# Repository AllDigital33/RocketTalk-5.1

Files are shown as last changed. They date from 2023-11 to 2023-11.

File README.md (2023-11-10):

# Rocket Talk v5.1

This is a full-featured rocket flight computer for amateur and experimental rocketry that incorporates radio telemetry, GPS tracking, staging, pyro event control, FTS, camera control, and more.

Please read the Overview.PDF file attached for a detailed overview of the hardware and software solution.

The code in the repository is split between the vehicle code (Arduino / Teensy) and the base station code (iPad / iOS Swift). 

# Disclaimer

We started this radio telemetry project in 2016 to better track our rockets in the skies over the Mojave desert. It has gone through a dozen hardware iterations and over fifty test flights. We always intended to share it and open source it, but projects like these are never complete. There is lots of room for improvement.

We’ve decided to take a snapshot and share our progress, so student groups and other amateurs can learn, borrow, or reuse some of our ideas and our sloppy code.

We owe a lot to the rocketry community, the TRF board, and student groups out at FAR that have shared their ideas, code, and practices to make our project and launches better and safer. 

This was never meant to be or become a commercial project, so please don't ask. The components and approach are way more expensive than any other trackers on the market, so you are not saving money by building your own. The EggTimer, TeleMega, and many more solutions are reliable and battle tested solutions.

This is a passion project to create bi-directional telemetry, long-range tracking, and an easy to use iPad based field solution.  

# Summary

**VEHICLE BOARD:**
* Teensy 4.1 MCU (ARM M7)
* GPS
* Barometer
* Two Accelerometers
* Gyroscope
* Pyro relays x 4
* Camera power control
* 64Mb of flash storage + SD transfer
* Temperature monitoring
* Voltage monitoring
* Bi-directional radio comms / 1W LoRa 433 Mhz 

**IPAD HANDHELD BASE STATION:**
* Simple touch-based UI for data and tracking
* Voice (siri like) event and alert reporting
* Local base GPS 
* Magnetometer / bearing
* Satellite mapping (Apple Maps)
* Local logging and file storage 
* Wifi/Internet
* Bi-directional radio comms / 1W LoRa 433 Mhz

# Vehicle Board Current Technology Choices

* **Teensy 4.1:**  The T4.1 with its Arm Cortex-M7 is just insanely fast for an MCU and it is loaded with a lot of versatile GPIO. We started our project on other Arduino based MCUs. Our last one was the ESP32. In benchmarks, an ESP32 can increment an integer about 700K times a second. That seems fast until you see the T4.1 (or 4.0) increment an integer 242 million times a second (wowzers!). This provides for almost unlimited CPU cycles for anything you can dream up during flight. The real limitation becomes the I2C bus, communication speeds, serial speeds, etc.  
* **Flash Memory:** The T4.1 has a built-in SD card that we used for years for logging data, but ultimately we had too many SD errors during flight that crashed the logging thread, so we switched to a 64 Mb flash chip (W25Q512JV) or 256mb (W25N02KVZEIR). The flash chip solders to the Teensy 4.1 and we're using the native LittleFS file system that uses the flash memory similar to a SD card. For easy transfer of data to SD there is a utility sketch that can be run after the flight. 
* **GPS:**  We are using the Ublox Max-M10S with serial communication. The M10S has proven to be an exceptional GPS, especially when combined with a Maxtena Helicore antenna. We run the GPS serial ttl instead of I2C, so we can save our I2C bus for sensor sampling. These GPS units are still under ITAR regulations, so they have limitations above 100K (more research needed).
* **GPS Antenna** The Maxtena Helicore M1575HCT-22P-SMA antenna is a passive GPS antenna capable of locking in 24+ satelites before launch.  
* **Barometer:**  We are using the TE MS5607 barometer on I2C sampling at 40Hz. We were using the BME280, but found it very susceptible to RF interference. The MS5607 has been reliable (no RFI), tracks up to 110K feet in the baro chamber, but it has a noisier signal, especially on descent. We also have to do some code gymnastics to sample at 40 hz and allow the sampling thread (and I2C bus) to stay free.
* **Accelerometers:** We have an Analog Devices ADXL375 200G accelerometer and a ST LSM6DSO32 32G accelerometer. The 200G is good to catch all the really big stuff and we often exceed the 32G’s of the LSM6DS, but the LSB resolution is not as good in a 200G setting, so the ST provides better resolution and accuracy below 32G’s. We are sampling the accelerometers and the gyro at 400 hz on the I2C bus.
* **Gyro:** The ST LSM6DSO32 also has a built-in gyroscope. We are using that, along with quaternions to calculate the rocket attitude (tilt).
* **Radios:**  We have tried a number of different radios, but we are very happy with our 1 watt LoRa radios on 433 Mhz (==FCC amateur radio license required==). You can get similar radios in 900 Mhz that don’t require a license. But, you are in this deep, so take the time to get a license. We use the LoRa 6100Pro serial TTL radios from NiceRF in China. The Lora technology is great, as we can create a mesh network and add a third radio on a tower to act as a repeater. These have proven to be reliable up to 15 miles “peak to peak” on the ground (mountain test) and I’m certain they will go to 100K+ feet in the air with the right antennas.
* **Downlink Antenna:**  The choice of downlink antennas on the vehicle is almost more important than the radio. We’ve tried dozens of antennas. The best antenna for us is a simple homemade dipole antenna running vertical in the airframe. We’ve tried whip, inverted V, fractal, and more, but the dipole performs the best. We used to make them by hand, but now we print our diploe antennas onto a long thin custom PCBs and trim to tune them (about $2/each)
* **5V Regulator:**  We use two L4941BDT-TR 5v 1A regulators to power the Teensy and the Radio. We run a separate regulator for the radio to minimize RFI and RF blowback, as well, provide the radio with a full one amp of power. All of the pyro events are triggered directly off of the Lipo battery and do not go through the regulators. 
* **Pyro Drivers:** We are using Rohm BV1HD090FJ-CE2 automotive switching drivers for all of our pyro events. These are rated at 5.5A and provide over-current protection and they have a convenient status pin that provides continuity check back to the MCU. There are other drivers that can switch up to 10A, but these have served us well for hundreds of pyro events using commercial MJG e-matches.
* **Terminals:**  We use JST board connectors for the low voltage connections and screw terminals for the hazard connections (power, switch, pyros).
* **RFI Shielding:**  A powerful one watt downlink transmitter comes with benefits and issues. On the positive, it can drive a data signal loud and far, but on the negative side it also showers all the sensors, the I2C lines, and the MCU with lots of disruptive radio frequency interference. In earlier versions we had sensor issues, code execution glitches, and full core dumps due to RFI. So, the current v5.1 board incorporates extensive shielding measures to protect the sensors and the MCU including full RF shield, ferrites, PCB ground planes, and more.

# Vehicle Board Code Overview

The Teensy code is built from a single C sketch in the Arduino (Teensyduino) IDE. It utilizes some external libraries for sensors, but is otherwise self-contained in a single code file. 

The code is partitioned into three Teensy threads, mimicking three separate infinite looping cores. The three threads share global variables, but are otherwise completely autonomous. Given the CPU speed, there is very little noticeable blocking between threads. Individual timers are used to trigger checks and activity within each loop.

**MAIN LOOP**
* Phase Logic (for each stage of flight)
* GPS check and transmit
* Transmit flight telemetry data
* Check voltage
* Check for separation events
* Check continuity
* Fire pyros and staging logic
* Radio receive processing 

**SAMPLE LOOP**
* Sample ADXL375 accelerometer at 400 Hz
* Sample LSM6DSO32 Accelerometer at 400 Hz
* Sample LSM6DSO32 Gyro at 400 Hz
* Compute Quaternion Tilt at 400 Hz
* Sample Barometer at 40 Hz

**LOGGING LOOP**
* Continuous logging to flash file system at various rates
* Logging flight and event data at 20 Hz
* Logging GPS data
* Logging radio TX/RX data
* Logging flight summary data

**PHASES:**

**STARTUP:** Power up sequence. Wait for GPS lock. Warm-up and characterize the Barometer. Bias adjust the Accelerometers.
**WAITING:**  Waiting for launch. Calibrate the Barometer. Bias adjust the Accelerometers.
**LAUNCH:**   Increase sample logging rate. Watch for and trigger staging lock-out and pyro events. Watch for Apogee and fire drogue pyro. 
**DESCENT:**  Reduce logging after 20 seconds. Watch for main altitude and fire main pyro. Watch for landing using barometer.
**LANDED:**   Log and transmit flight summary. Idle logging and transmitting.
**BASIC:**    Exception safe mode (activated by base) with no event triggering, just sampling, logging, and transmitting flight/gps data.

# iPad Base Station Technology Choices

* **iPad Mini:**  In earlier versions, we built the handheld base station from an Arduino and an LCD. This worked, but integrating the GPS and a magnetometer for tracking proved messy at best (field calibrating the magnetometer for an accurate bearing was not fun). So, we decided to switch over to an iPad mini, using Apple’s Swift development code to build the application and UI.  After a few days of “hello world” building, Swift was a dream compared to building hardware. Pulling base coordinates to compare to vehicle coordinates only required one line of code. Magnetic bearing was only one line of code. Voice event announcements only one line of code. Maps drop right in. Everything was just so much easier. That said, this does require a cellular iPad mini (no plan required), as those are the only iPads with actual GPS hardware. Also, we needed to use a proprietary lightening to RS232 serial cable (Redpark serial cable) to interface with the radio. And the radio needs its own little companion box with a battery. 
* **Redpark Serial Cable:**  This cable and the iOS Swift libraries is required to interface the iPad to the LoRa serial radio. It is RS232 serial, so a small RS232 to TTL converter is also used before connecting to the radio. There are not many ways to interface an Apple iOS device directly to serial communications. This one works great. A note:  You cannot distribute apps in the Apple App Store that use the RedPark cable. It can only be used with developer apps or enterprise app distribution.
* **Bluetooth Serial Option:**  We use the same iPad-Radio approach for other projects, including a liquid GSE project. In those projects we have switched away from using the Redpark cable and instead use a ESP32 as a "bluetooth bridge" between the iPad and the Serial LoRa radio. We have found it to be as good if not more reliable and allows for easier bench testing. Eventually, we will move the code over to this RocketTalk project to support that bridge.
* **Radios:**  We use the exact same radio as the vehicle radio. The LoRa 6100Pro serial TTL radios from NiceRF in China. We have tested these point-to-point at 14 miles on the ground.
* **Antenna:**  We are using an Arrow II handheld Yagi antenna (440-3) for good directional reception.
* **Additional mounting components:** To make a great one-handed tracker, we mount the iPad onto a UZOPI Mavic Mini Air Pro Platinum Spark Accessories Tablet Holder and we bolted the antenna and a camera pistol grip to the holder. The radio, battery, and cable are in a small project box attached to the holder plate.

# iPad Application Overview

The iPad application is written in xCode using Swift, Apple's native app development language. In the main storyboard file you will see it is entirely in a tab view controller with eight different tabs or views. The global variables and functions are in the AppDelegate file, but all other code is in the view controllers for each tab screen. The redPark serial communication callback for the radio is in the first "main" tab view, since it always appears first. The screen views are as follows:

* **Main:**  This is the primary screen for viewing flight data, event data, continuity status, GPS location/distance/bearing/azimuth, and a dozen other indicators. Flight data and GPS data is updated independently, based on what is received over the radio.
* **Tracking:**  This view has the same directional arrow, distance, bearing, azimuth, etc., but also includes an Apple Maps satellite location view and allows for tracking from a) live radio data 2) the local file log or 3) from a manual entry. Both Main and tracking use the iPad GPS data and compass to calculate distance and bearing. 
* **Send:** This view allows you to send commands to the rocket in flight to fire pyros, get additional status, force it into phases or modes, and FTS.
* **Booster:**  The application is setup, so you can track both a sustainer and booster using the same radio. Booster data (flight data and GPS) come in to the booster view, along with event (pyro/separation/continuity) data. The Booster uses a mini version of the vehicle board that still includes a barometer, accelerometer, gyro, GPS, and radio.
* **Summary:** The summary screen gets populated after a successful landing with additional data sent from the vehicle. The flight summary data includes speed, acceleration, flight time, distance, max tilt, and dozens of other flight measurements. 
* **Setup:**  This view allows you to configure alarms and alerts. The application provides voice alerts for things like high rocket descent speed, rocket descending directly overhead, high temperature, battery warnings, tilt warnings on launch, etc.
* **Files:**  This view allows you to manage and view base station log files for flight data, GPS data, radio data, and flight summary information. Log files can also be exported or emailed from this screen. 
* **Radio:**  This view provides a real-time monitor for radio traffic. Radio transmissions are in ascii, comma delimited sentences with specific start and stop characters and other checksum conditions. Real-time radio monitoring is usually just for diagnostic or troubleshooting purposes.

# Other

**CUSTOM PCB**
We started the first versions of this four years ago on breadboards, but quickly realized breadboards don't hold up to the extremes of rockets very well. We found that using EasyEDA to create the schematic and then generate the board design was a good way to make the design accessable to everyone without expensive PCB software licenses. EasyEDA and JCLPCB make it really easy to design a circuit, trace the PCB, and print it for cheap. The source EasyEDA files are included in the hardware folders. 

**CUSTOM 3D PRINTED SLEDs**
We have made dozens of different sleds for 3", 4", and 8" rockets using the online version of Sketchup. We've included the 3" vehicle sled files in the vehicle folder for reference. We also included the base station radio project box files for reference, but those are probably better replaced with a simple off the shelf project box.  

Thank you to everyone that has contributed and offered advice along the way. 

May your rockets fly straight and high and may you always know exactly where they are.

Mike & Preston

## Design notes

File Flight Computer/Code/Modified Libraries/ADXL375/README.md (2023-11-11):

# shockduino

The idea is to create a small device that you can include in a package/parcel sent via the post. 
 
The device will be capable of detecting shock/drop events. Before signing for the parcel at the other end you can see if it's been dropped or not.

## Hardware

Initially using an [RFduino](http://www.rfduino.com/) and an [ADXL375](http://www.analog.com/en/products/mems/mems-accelerometers/adxl375.html) accelerometer.

### Prototype

The prototype design is using an [RFduino dev board](http://www.rfduino.com/product/rfd22102-rfduino-dip/index.html), [RFduino USB shield](http://www.rfduino.com/product/rfd22121-usb-shield-for-rfduino/index.html) and an [ADXL375Z eval board](http://www.analog.com/en/design-center/evaluation-hardware-and-software/evaluation-boards-kits/EVAL-ADXL375.html) all slung together on a prototyping breadboard.

Connections between the RFduino and ADXL375:
- Ground is common
- 3.3v from the RFduino is connected to VIO and VS 
- SCL is connected between GPIO pins 3,4,5,6 to SDO,SCL,SDA,CS

## Project Plan

### Prototype Hardware

- [x] Connect up hardware and verify it works

### Prototype Software

- [x] Pull meaningful data from the ADXL375
- [x] Separate out ADXL375 functionality into a library
- [x] Implement shock detection on the ADXL375
- [x] Record detailed accelleration data after a shock event is triggered
- [x] Return maximum shock amplitude after a shock has occurred
- [x] Make configurable shock detection interface simple
- [x] Get iBeacon reporting of shocks working
- [ ] Get RFduino sleep mode and interrupt on shock event working
- [ ] Get INACT/ACT detection working with ADXL375
- [ ] Configure iBeacon to only advertise when the ADXL375 is active
- [ ] Allow RFduino to detect issues and power cycle ADXL375

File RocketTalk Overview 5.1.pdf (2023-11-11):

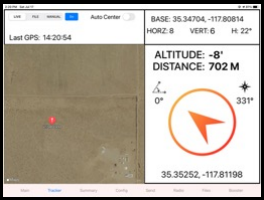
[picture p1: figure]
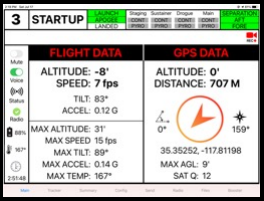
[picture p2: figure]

# Flight Telemetry, Tracking, and Deployment System

## Version 5.1 – November 2022

## Disclaimer:

We started this radio telemetry project in 2016 to better track our rockets in the skies over the Mojave desert. It has gone through a dozen hardware iterations and over fifty test flights. We always intended to share it and open source it, but projects like these are never complete. There is lots of room for improvement.

We’ve decided to take a snapshot and share our progress, so student groups and other amateurs can learn, borrow, or reuse some of our ideas and our sloppy code.

We owe a lot to the rocketry community, the TRF board, and student groups out at FAR that have shared their ideas, code, and practices to make our project and launches better and safer.

Please pay it forward.

Mike & Preston

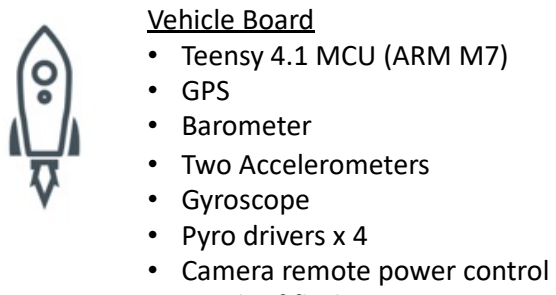
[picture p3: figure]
Vehicle Board; • GPS • Barometer • Two Accelerometers • Gyroscope • Pyro drivers x 4 • Camera remote power control

- Teensy 4.1 MCU (ARM M7)
- 64Mb of flash storage + SD transfer
- Temperature monitoring
- Voltage monitoring
- Bi-directional radio comms / 1W LoRa 433 Mhz

Base (handheld) iPad Mini
- Simple touch-based UI for data and tracking
- Voice event reporting
- Local base GPS
- Magnetometer / bearing
- Satellite mapping
- File storage
- Wifi/Internet
- Bi-directional radio comms 1W LoRa 433 Mhz

Optional Radio Repeater

Mesh network repeater
5W LoRa 433 Mhz

# RocketTalk

# VEHICLE BOARD

# Vehicle Board – Conceptual Architecture

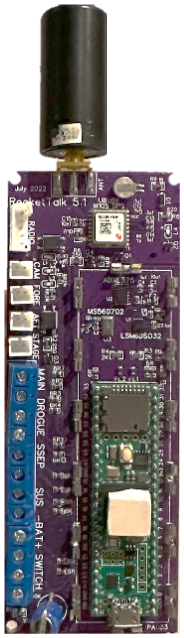
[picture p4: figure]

## Teensy

4.1

ADXL375
200G
Accelerometer

MS5607
Barometer

LSM6DSO32
Accelerometer
and Gyro

64Mb Flash
Memory
W25Q512JV

Built-in
SD card

I2C Bus

Ublox
Max M10S
GPS
NiceRF | Serial TTL
LoRa 6100Pro
433 Mhz Radio

Serial TTL

5V DC
Linear
Regulator

7.4VDC
Lipo
Battery

5V DC
Linear
Regulator

Cam

Four 5.5A Rohm High-side Drivers for Pyro Events

Two opto relays for camera switching and radio switching

JST

External

External

GPIO Pins

JST | JST | JST

JST

Three external switches to detect separation events

Helical GPS
Antenna

Current Technology Choices – Vehicle Board • Teensy 4.1: The T4.1 with its Arm Cortex-M7 is just insanely fast for an MCU and it is loaded with a lot of versatile GPIO. We started our project on other Arduino based

MCUs. Our last one was the ESP32. In benchmarks, an ESP32 can increment an integer about 700K times a second. That seems fast until you see the T4.1 (or 4.0) increment an integer 242 million times a second (wowzers!). This provides for almost unlimited CPU cycles for anything you can dream up during flight. The real limitation becomes the I2C bus, communication speeds, serial speeds, etc. The T4.1 also has a built-in SD card for easy transfer of data. And it easily accommodates a 64mb flash chip (W25Q512JV). We log directly to the 64mb flash chip for more reliable 50-100hz logging and then copy to SD after flights for easy transfer to a computer.

- GPS: We are using the Ublox max M10S with serial communication. The performance of the M10S has been incredible. We often have 24+ satellites fixed while on the pad. We run the GPS serial ttl instead of I2C, so we can save our I2C bus for sensor sampling. These GPS units are still under ITAR regulations, so they have Cocom limits above 150K feet and above specific velocities. The v5.1 board has an SMA connector for the GPS, so we use a Maxtena Helicore M1575HCT-22P-SMA antenna instead of a narrowly focused patch antenna. The combination of M10S with an omnidirectional antenna has produced far more reliable results.
- Barometer: We are using the TE MS5607 barometer on I2C sampling at 40Hz. We were using the BME280, but found it very susceptible to RF interference. The MS5607 has been reliable (no RFI issues), tracks up to 110K feet in the baro chamber, but it has a noisier signal, especially on descent. We also have to do some code gymnastics to sample at 40 hz and allow the sampling thread (and I2C bus) to stay free.
- Accelerometers: We have an Analog Devices ADXL375 200G accelerometer and a ST LSM6DSO32 32G accelerometer. The 200G is good to catch all the really big stuff and we often exceed the 32G’s of the LSM6DS, but the LSB resolution is not as good in a 200G setting, so the ST provides better resolution and accuracy below 32G’s. We are sampling the accelerometers and the gyro at 400 hz on the I2C bus.
- Gyro: The ST LSM6DSO32 also has a built-in gyroscope. We are using that, along with quaternions to calculate the rocket attitude (tilt).
- Radios: We have tried a number of different radios, but we are very happy with our 1 watt LoRa radios on 433 Mhz (FCC amateur radio license required). You can get similar radios in 900 Mhz that don’t require a license. But, you are in this deep, so take the time to get a license. We use the LoRa 6100Pro serial TTL radios from NiceRF in China. The Lora technology is great, as we can create a mesh network and add a third radio on a tower to act as a repeater. These have proven to be reliable up to 15 miles “peak to peak” on the ground (mountain test) and I’m certain they will go to 100K+ feet in the air with the right antennas.
- Downlink Antenna: The choice of downlink antennas on the vehicle is almost more important than the radio. We’ve tried dozens of antennas. The best antenna for us is a simple homemade dipole antenna running vertical in the airframe. We’ve tried whip, inverted V, fractal, and more, but the dipole performs the best. We used to make them by hand, but now we print our diploe antennas onto a long thin custom PCBs and trim to tune them (about $2/each).

Current Technology Choices – Vehicle Board • 5V Switched Regulator: We use two L4941BDT-TR 5v 1A regulators to power the Teensy and the Radio. We run a separate regulator for the radio to minimize RFI and RF

blowback, as well, provide the radio with a full one amp of power. All of the pyro events are triggered directly off of the Lipo battery and do not go through the regulators.

- Opto-Relays: We are using the Toshiba TLP3553A SSR 4A opto relays to provide optoisolated switching for the radio power and to turn on-off the camera.
- Terminals: We use JST board connectors for the low voltage connections and screw terminals for the hazard connections (power, switch, pyros).
- RFI Shielding: A powerful one watt downlink transmitter comes with benefits and issues. On the positive, it can drive a data signal loud and far, but on the negative side it also showers all the sensors, the I2C lines, and the MCU with lots of disruptive radio frequency interference. In earlier versions we had sensor issues, code execution glitches, and full core dumps due to RFI. So, the current v5.1 board incorporates extensive shielding measures to protect the sensors and the MCU:
- Full RF shielding cover top and bottom: Used Wurth Electronics DIY Shielding (360002) and Leader Tech TC-01 clips.
- Ferrite beads inline with the I2C signals: Part BLM21SP102SH1D
- Ferrite beads on the sensor VCC lines: TDK MPZ1608S101ATDH5
- Small resistors on GPIO pins: 33 ohm resistors on GPIO pins
- Added brown-out capacitor: 4F Vishay MAL219691104E3
- Grounded unused GPIO pins
- Significant copper ground infill under and across MCU and sensors
- Note: The GPS chip is already shielded, so did not require special consideration

# Vehicle Board – Custom PCB

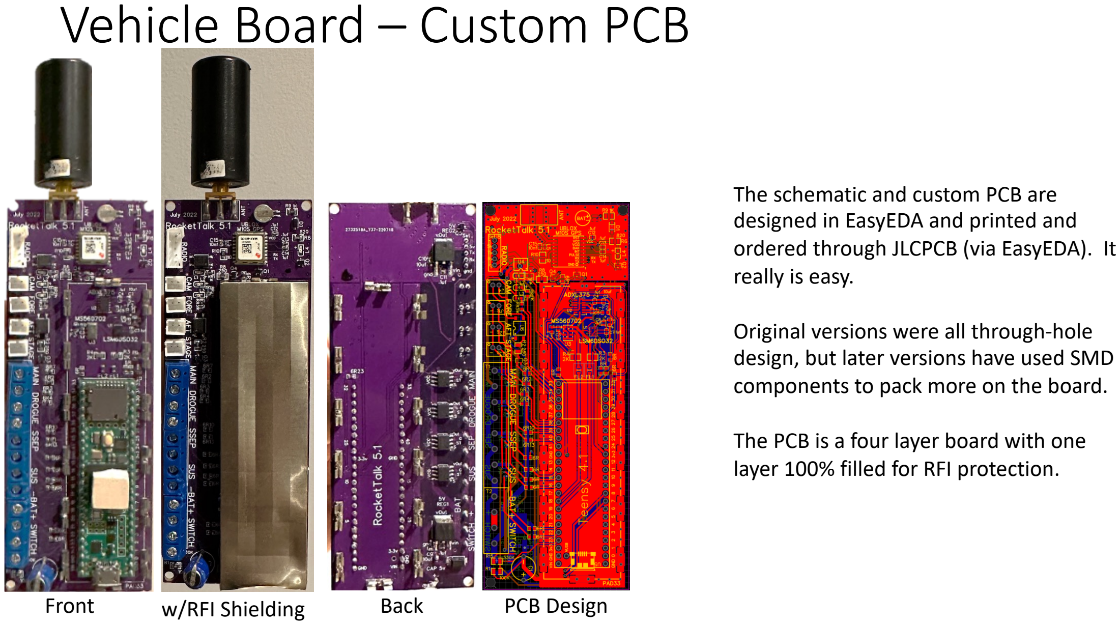
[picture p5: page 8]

## The schematic and custom PCB are designed in EasyEDA and printed and ordered through JLCPCB (via EasyEDA). It

really is easy.

## Original versions were all through-hole design, but later versions have used SMD

components to pack more on the board.

## The PCB is a four layer board with one

layer 100% filled for RFI protection.

Front | w/RFI Shielding | Back | PCB Design

# Vehicle Board – Code Design

The Teensy code is built from a single C sketch in the Arduino (Teensyduino) IDE. It utilizes some external libraries for sensors, but is otherwise self-contained in a single code file.

The code is partitioned into three Teensy threads, mimicking three separate infinite looping cores. The three threads share global variables, but are otherwise completely autonomous. Given the CPU speed, there is very little noticeable blocking between threads. Individual timers are used to trigger checks and activity within each loop.

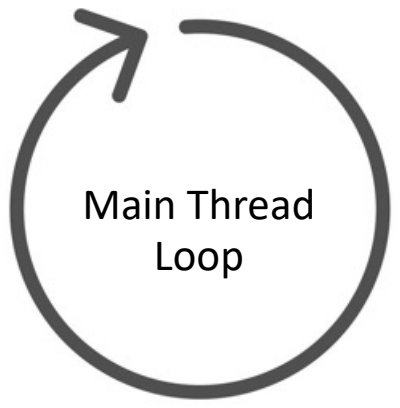
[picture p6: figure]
Main Thread Loop

- Phase Logic (for each stage of flight)
- GPS check and transmit
- Transmit flight telemetry data
- Check voltage
- Check for separation events
- Check continuity
- Fire pyros
- Radio receive processing
- Sample ADXL375 at 400 Hz
- Sample LSM6DSO32 Accel at 400 Hz
- Sample LSM6DSO32 Gyro at 400 Hz
- Compute Quaternion Tilt at 400 Hz
- Sample Barometer at 40 Hz
- Continuous logging to flash file system at various rates
- Logging flight and event data at 20 Hz
- Logging GPS data
- Logging radio TX/RX data
- Logging flight summary data

# Vehicle Board – Code Design

STARTUP | Power up sequence. Wait for GPS lock. Warm-up and characterize the Barometer. Bias adjust the Accelerometers.
WAITING | Waiting for launch. Calibrate the Barometer. Bias adjust the Accelerometers.
LAUNCH | Increase sample rate. Watch for and trigger staging pyro events. Watch for Apogee and fire drogue pyro.
DESCENT | Reduce logging after 20 seconds. Watch for main altitude and fire main pyro. Watch for landing using barometer.
LANDED | Log and transmit flight summary. Idle logging and transmitting.
BASIC | Exception mode (activated by base) with no event triggering, just sampling, logging, and transmitting flight/gps data.

## Flight Phase

# Vehicle Board

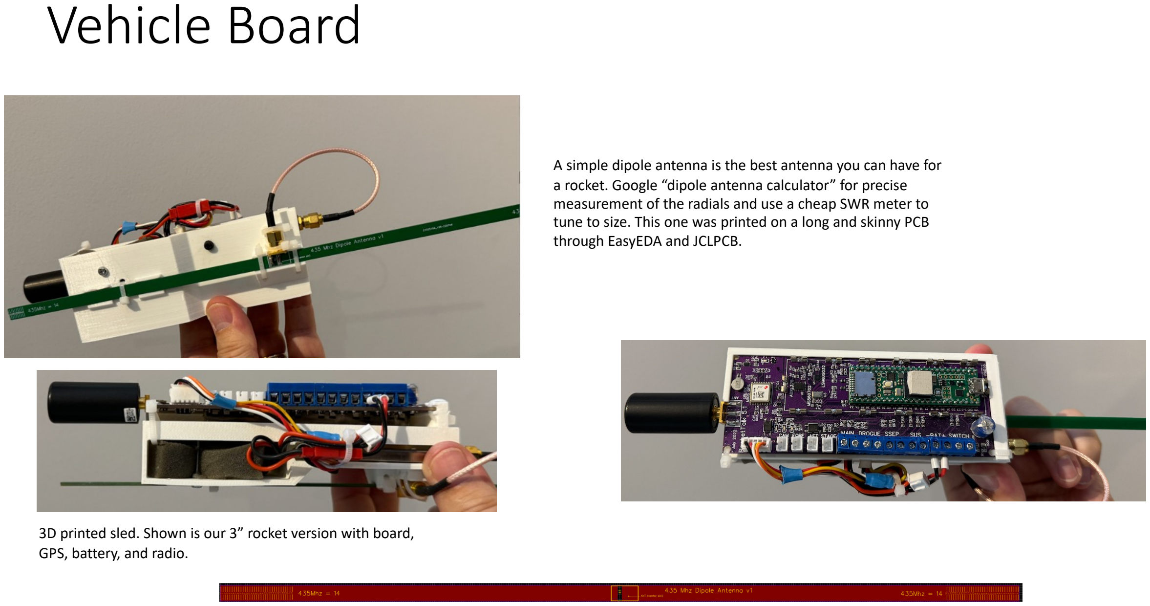
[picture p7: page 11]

A simple dipole antenna is the best antenna you can have for a rocket. Google “dipole antenna calculator” for precise measurement of the radials and use a cheap SWR meter to tune to size. This one was printed on a long and skinny PCB through EasyEDA and JCLPCB.

3D printed sled. Shown is our 3” rocket version with board, GPS, battery, and radio.

# RocketTalk

# BASE STATION iPAD

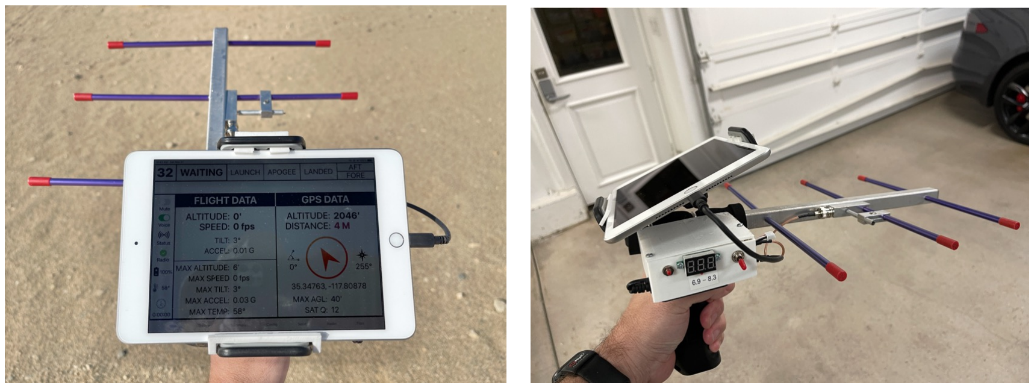
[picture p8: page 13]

Current Technology Choices – Base Station • iPad Mini: In earlier versions, we built the handheld base station from an Arduino and an LCD. This worked, but integrating the GPS and a magnetometer for tracking proved

messy at best (field calibrating the magnetometer for an accurate bearing was not fun). So, we decided to switch over to an iPad mini, using Apple’s Swift development code to build the application and UI. After a few days of “hello world” building in Swift was a dream, compared to building hardware. Pulling base coordinates to compare to vehicle coordinates only required one line of code. Magnetic bearing was only one line of code. Voice event announcements only one line of code. Maps drop right in. Everything was just so much easier. That said, this does require a cellular iPad mini (no plan required), as those are the only iPads with actual GPS hardware. Also, we needed to use a proprietary lightening to RS232 serial cable (Redpark serial cable) to interface with the radio. And the radio needs its own little companion box with a battery.
- Redpark Serial Cable: This cable and the iOS Swift libraries is required to interface the iPad to the LoRa serial radio. It is RS232 serial, so a small RS232 to TTL converter is also used before connecting to the radio. There are not many ways to interface an Apple iOS device to serial communications. This one works great. A note: You cannot distribute apps in the Apple App Store that use the RedPark cable. It can only be used with developer apps or enterprise app distribution.
- Radios: We use the exact same radio as the vehicle radio. The LoRa 6100Pro serial TTL radios from NiceRF in China.
- Antenna: We are using an Arrow II handheld Yagi antenna (440-3) for good directional reception.
- Additional mounting components: To make a great one-handed tracker, we mount the iPad onto a UZOPI Mavic Mini Air Pro Platinum Spark Accessories Tablet Holder and we bolted the antenna and a camera pistol grip to the holder. The radio, battery, and cable are in a small project box attached to the holder plate.

# Base Station – Conceptual Architecture

## iPad Mini (cellular / no plan)

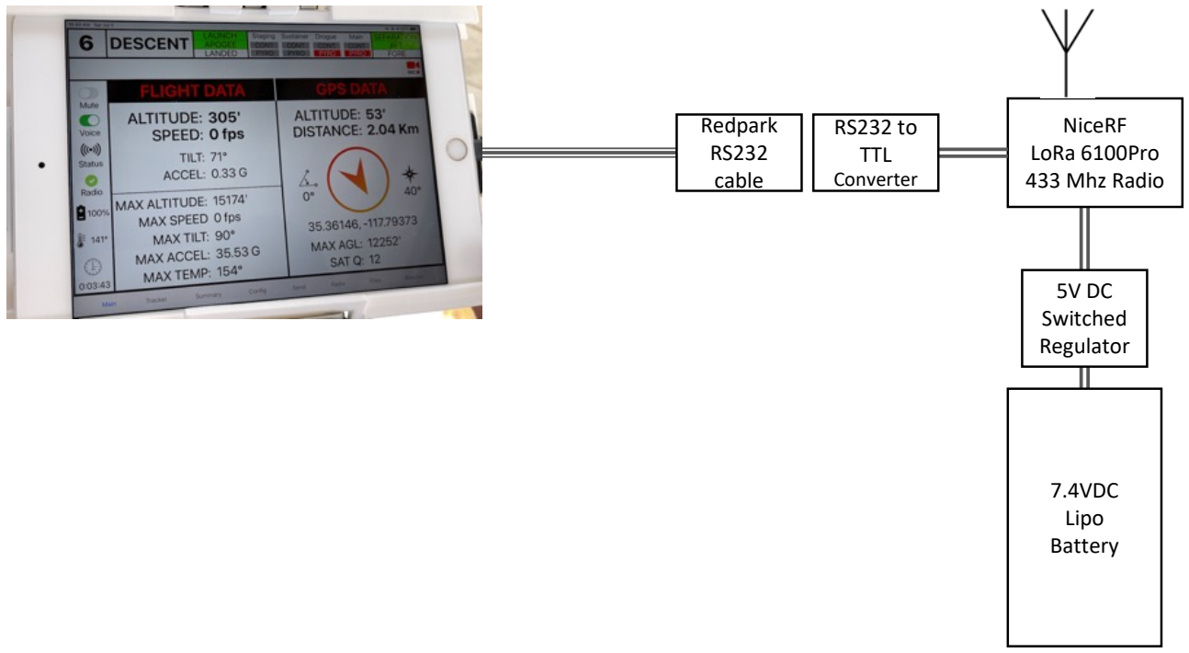
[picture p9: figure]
NiceRF LoRa 6100Pro 433 Mhz Radio; Redpark RS232 cable; 7.4VDC Lipo Battery; 5V DC Switched Regulator; RS232 to TTL Converter

# Base Station – Application Features

The native iOS application written in Swift uses a Tab View Controller with six tabs or screens that you can easily toggle between.

Main Screen
(Sustainer)

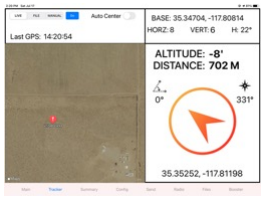
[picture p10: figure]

Tracking Screen
(Sustainer)
Transmit Screen | Booster Screen | Configuration

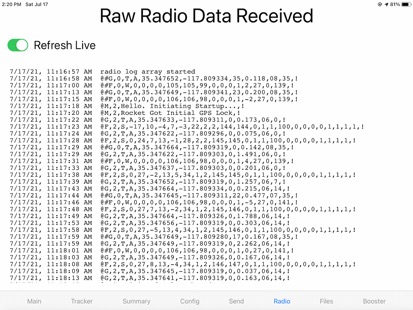
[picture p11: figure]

Log Files | Raw Radio Data

# Base Station – Application Features

The native iOS application written in Swift uses a Tab View Controller with six tabs or screens that you can easily toggle between.

Main Screen
(Sustainer)

Tracking Screen
(Sustainer)

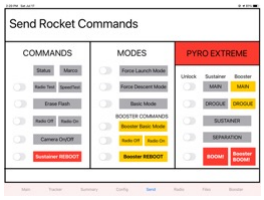
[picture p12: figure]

Transmit Screen | Booster Screen

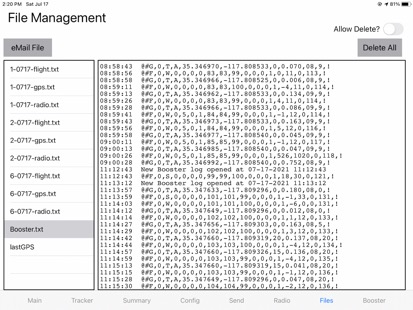
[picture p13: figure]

Configuration | Log Files | Raw Radio Data

# Base Station – Application Features

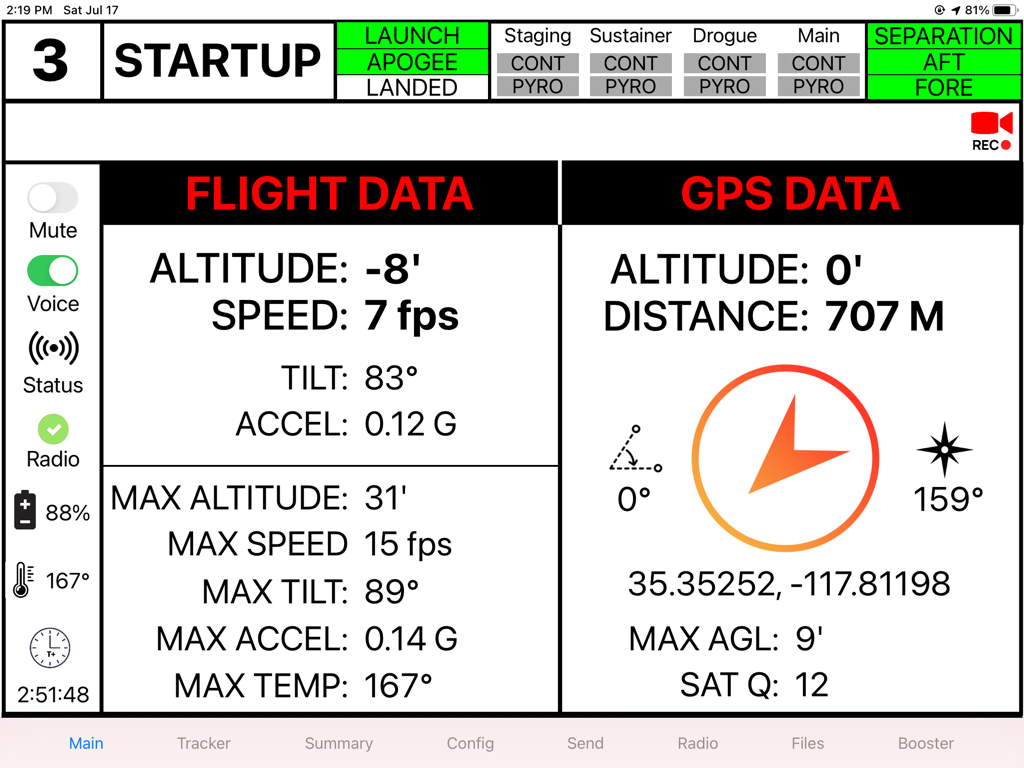
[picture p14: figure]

Phase event information, pyro continuity and fire confirmation, and separation events (using hall sensors)

GPS data provides altitude and distance, between the base and vehicle. It also provides bearing and azimuth angle and a large arrow direction indicator.

# Base Station – Application Features

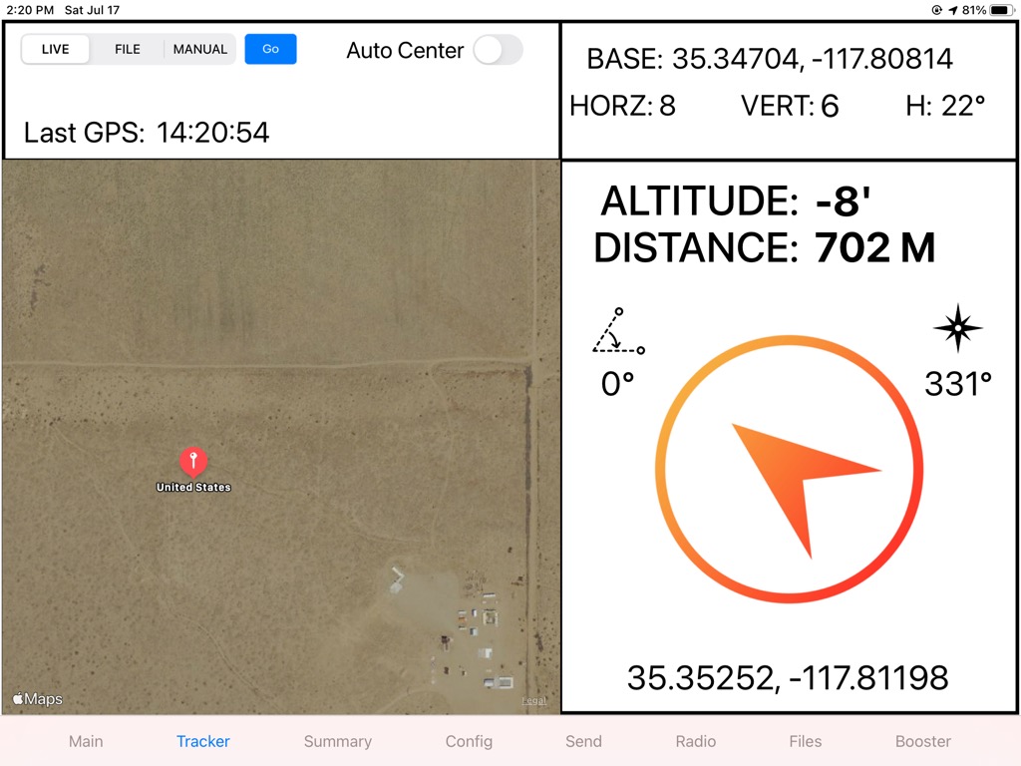
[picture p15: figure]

The tracking screen provides all the same GPS data, as well as satellite mapping.

Tracking also allows to pull location data live (from radio), from the log files, or by manually entering long/lat data.

# Base Station – Application Features

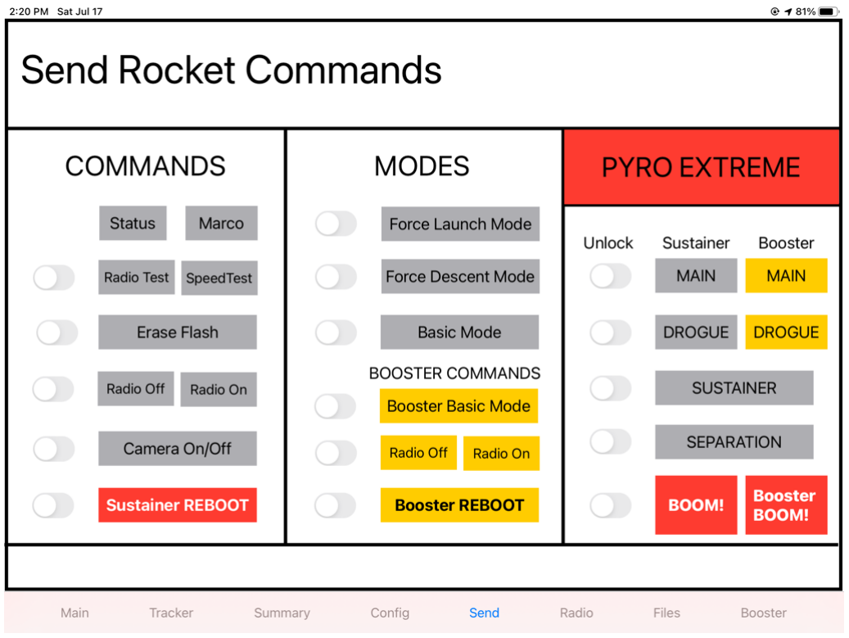
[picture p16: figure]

Commands can be sent to the sustainer or booster (separate vehicle board) for a number of different functions and modes.

Commands can be issued to manually fire the pyros or fire all the pyros (BOOM), as a poor mans FTS (flight termination system).

Flash can be erased, MCUs rebooted, radio TX can be turned off (good for speeding up GPS lock), etc.

# Base Station – Application Features

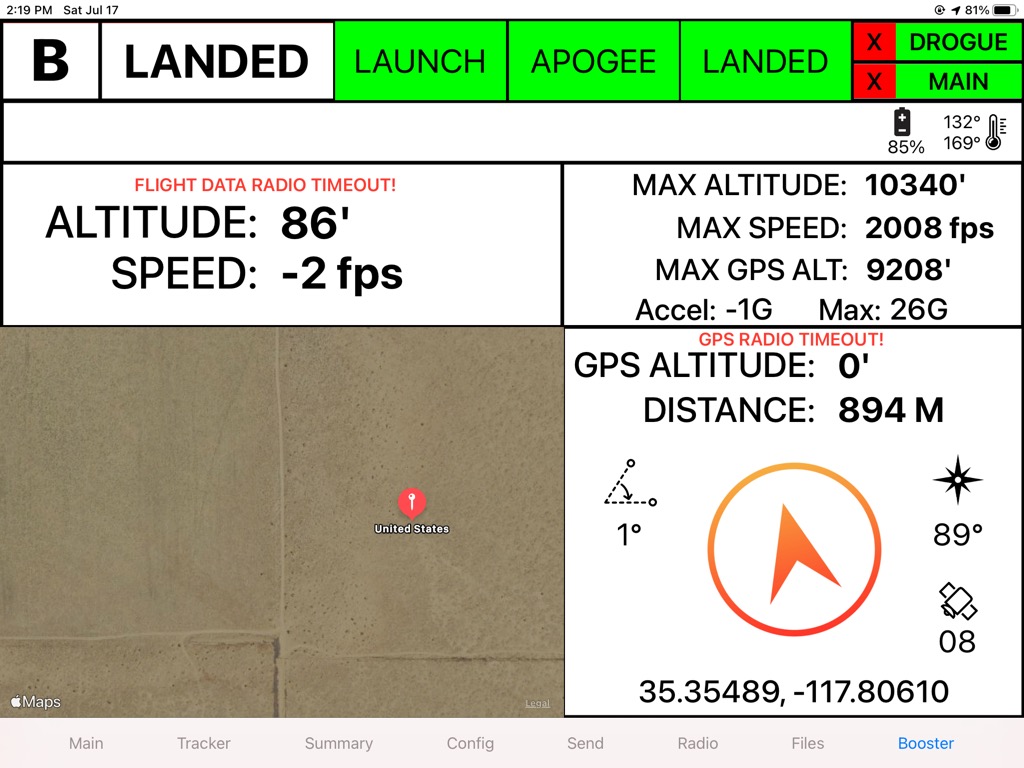
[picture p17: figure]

We have a smaller booster board that uses the same radio and frequency. So, we get both booster and sustainer reporting to the same iPad application.

The booster screen has a lot of the same flight data and GPS tracking information, along with phase, event, and continuity confirmation on the top.

# Base Station – Application Features

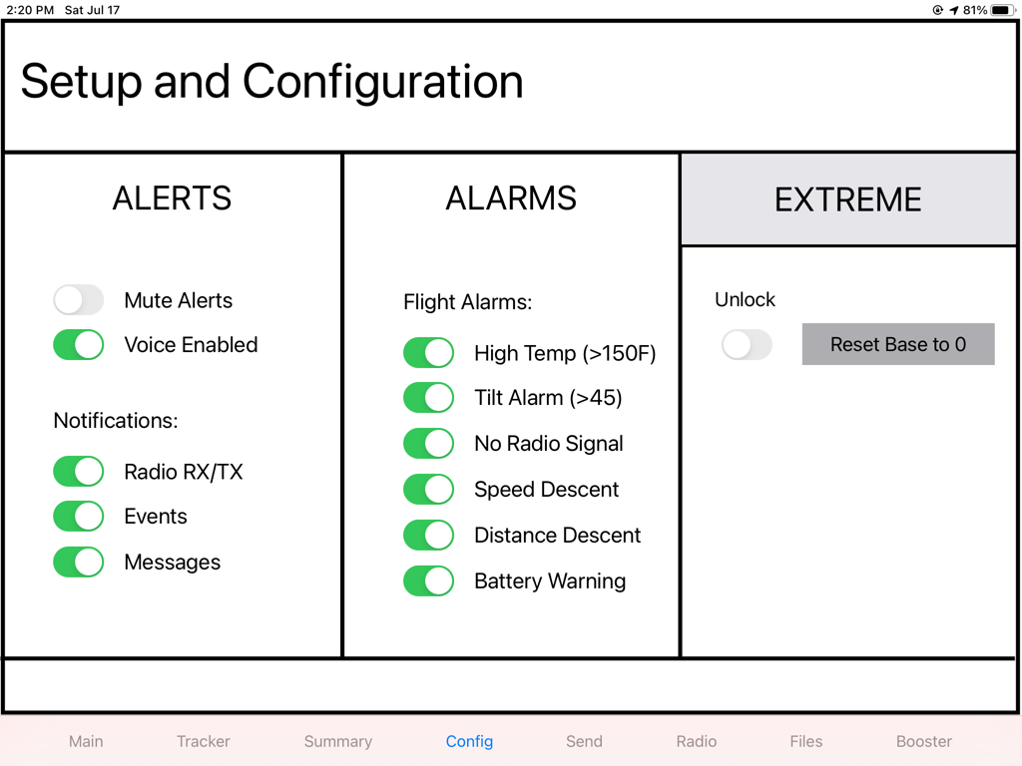
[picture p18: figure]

Basic settings for alerts and alarms

# Base Station – Application Features

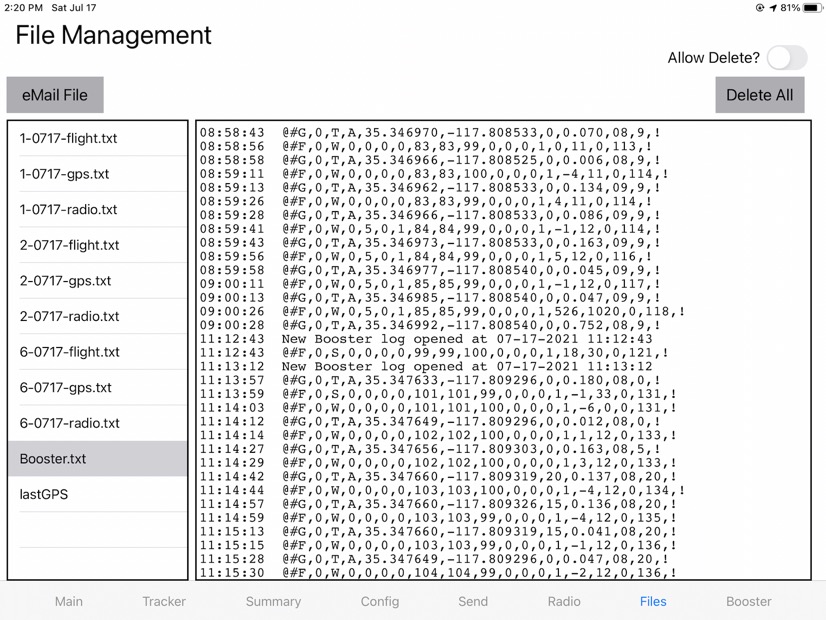
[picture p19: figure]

The base station logs all flight, GPS, and radio data. It logs Booster data separately. It also keeps a file for last know GPS locations.

# Base Station – Application Features

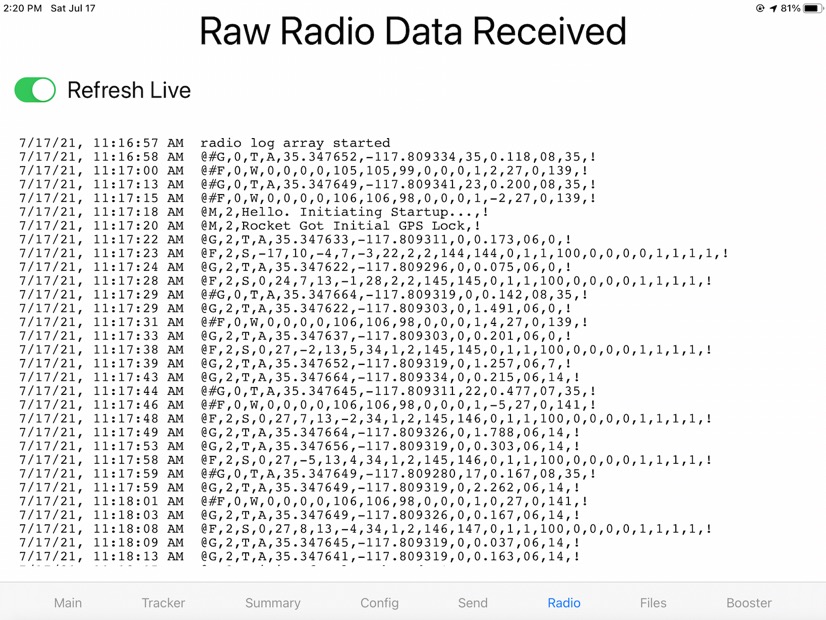
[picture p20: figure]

Radio data is transmitted in comma delimited sentences with a stop and start character. The radio screen allows reading the radio data in real-time to confirm activity at a more technical level. Generally, this is only used for
troubleshooting or diagnostics.

# RocketTalk

# OTHER

# Radio Repeater

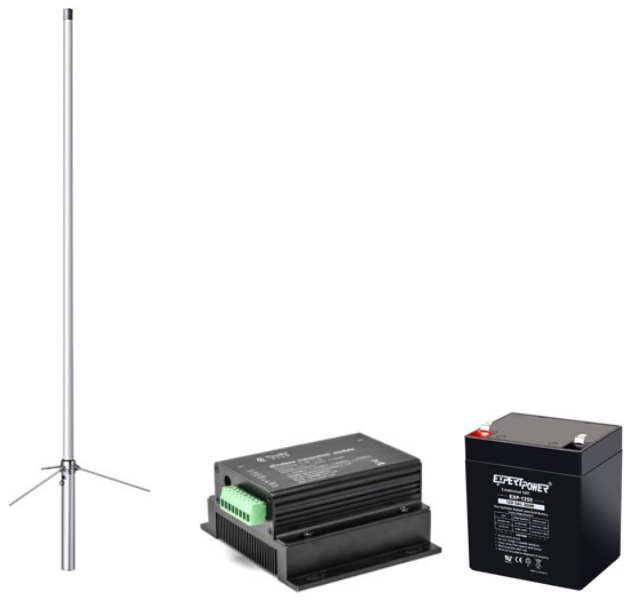
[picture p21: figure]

The beauty of LoRa radios is that they can be configured to work in “mesh” mode, as either nodes or repeaters. So, we have a NiceRF 5 watt LoRa6500Pro that we configure as a repeater on the same frequency and ID as our base and vehicle radios. Adding the repeater and putting an antenna high in a tower gives us exceptional range on the horizon (or in the dirt) with almost zero packet loss.

The repeater is passive, so the base and vehicle work just fine without it, but work even better when it is on.

We use a 4.5 foot Diamond X30A Dualband 2m/70cm Antenna with the repeater.

Booster Board | We have a mini version of the vehicle board that we use in
| the Booster. It is a subset of the main (sustainer) vehicle board, using a Teensy 4.0 (instead of 4.1), barometer, accelerometer/gyro, two pyro charge relays, a radio, and GPS.
| It has no logging capability and no 200G ADXL375 accelerometer. It also is using only one 5V regulator.
| This board uses the exact same radio, on the same frequency, so the handheld base station only needs one radio for both booster and sustainer communication.
| The code for the booster is a subset of the sustainer, although radio commands/sentences are all prefixed with #, to differentiate between the booster and sustainer.

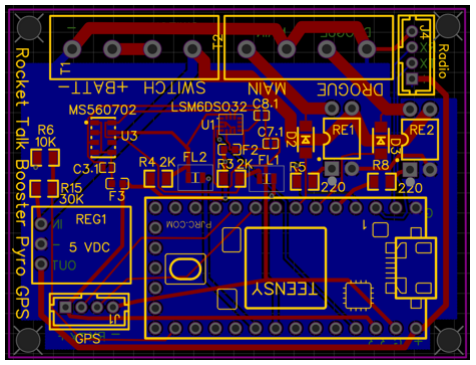
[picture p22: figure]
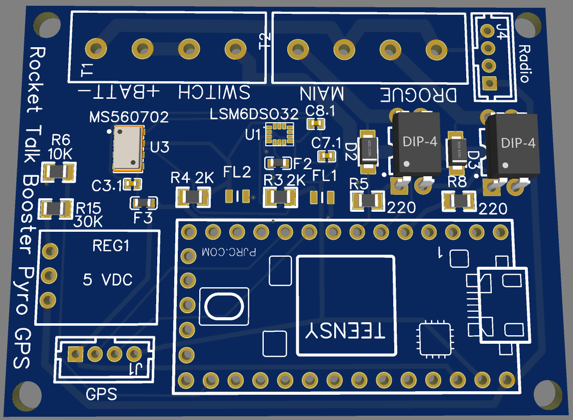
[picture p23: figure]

# RocketTalk

# PARTS REFERENCE

# Vehicle Components

Teensy 4.1 | https://www.pjrc.com/store/teensy41.html
“fully loaded” w/flash soldered | https://protosupplies.com/product/teensy-4-1-fully-loaded/
Ublox Max M10S GPS | https://www.digikey.com/en/products/detail/u-blox/MAX-M10S-00B/15712906
GPS Antenna M1575HCT-22P-SMA | https://www.mouser.com/ProductDetail/Maxtena/M1575HCT-22P-SMA
TE MS5607 barometer | https://www.digikey.com/catalog/en/partgroup/ms5607-02ba03/54690
ADXL 375 Accelerometer | https://www.digikey.com/en/products/detail/analog-devices-inc/ADXL375BCCZ/4376342
LSM6DS032 Accel/Gyro
| https://www.digikey.com/en/products/detail/stmicroelectronics/LSM6DSO32TR/11694177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
NiceRF Lora 6100Pro Radio | https://www.nicerf.com/products/detail/1w-lora-wireless-data-transmission-module-lora6100pro.html
Rohm BV1HD090FJ-CE2 driver | https://www.digikey.com/en/products/detail/rohm-semiconductor/BV1HD090FJ-CE2/10249266
Toshiba TLP3553A opto-relay | https://www.digikey.com/en/products/detail/TLP3553A(F/TLP3553A(F-ND/9472359
LD1117 5v regulator | https://www.mouser.com/ProductDetail/STMicroelectronics/LD1117DT50CTR?qs=6MdFBD70OtGoLwD4bsdGtg%3D%3D
Lipo Battery 7.4v 850 Mah | https://www.amazon.com/gp/product/B07P2PDVM5/ref=ppx_yo_dt_b_search_asin_title?ie=UTF8&psc=1
5v brown out cap (4F) | https://www.digikey.com/en/products/detail/vishay-beyschlag-draloric-bc-components/MAL219691104E3/5017510
Wurth DIY Shielding | https://www.digikey.com/en/products/detail/würth-elektronik/360002/10468233?utm_medium=email

# Base Components

iPad Mini 64GB Wifi/Cellular | https://www.amazon.com/gp/product/B07PQ8WX75/ref=ppx_yo_dt_b_search_asin_title?ie=UTF8&psc=1
Redpark Serial Cable | https://redpark.com/lightning-serial-cable-l2-db9v/
Serial RS232 to TTL | https://www.amazon.com/gp/product/B00OPTOKI0/ref=ppx_yo_dt_b_search_asin_title?ie=UTF8&psc=1
NiceRF Lora 6100Pro Radio | https://www.nicerf.com/products/detail/1w-lora-wireless-data-transmission-module-lora6100pro.html
Arrow II Antenna 440-3 | http://www.arrowantennas.com/arrowii/440-3ii.html
Tablet holder | https://www.amazon.com/gp/product/B071RK5FYY/ref=ppx_yo_dt_b_search_asin_title?ie=UTF8&psc=1
Camera Grip handle | https://www.amazon.com/gp/product/B07D3QDL1T/ref=ppx_yo_dt_b_search_asin_title?ie=UTF8&psc=1

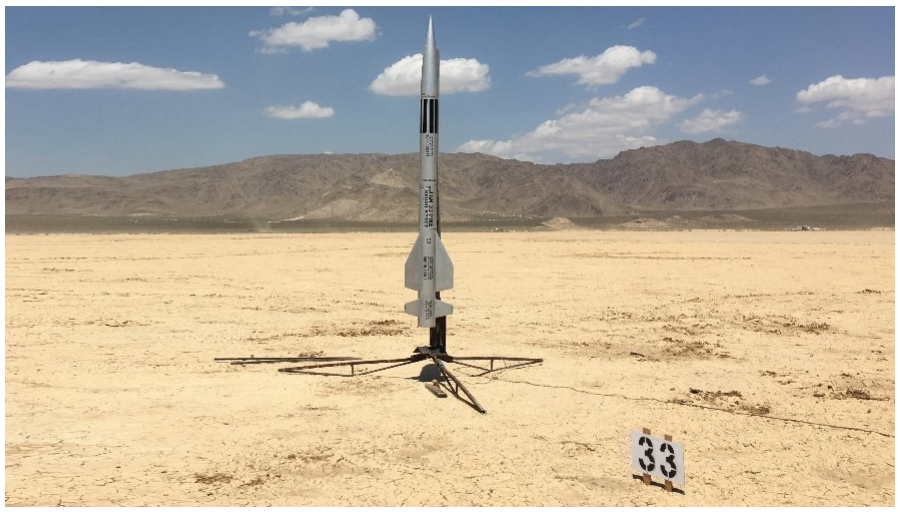
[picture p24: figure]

## Questions? @PAD33space on Twitter/X

## or @AllDigital on TRF

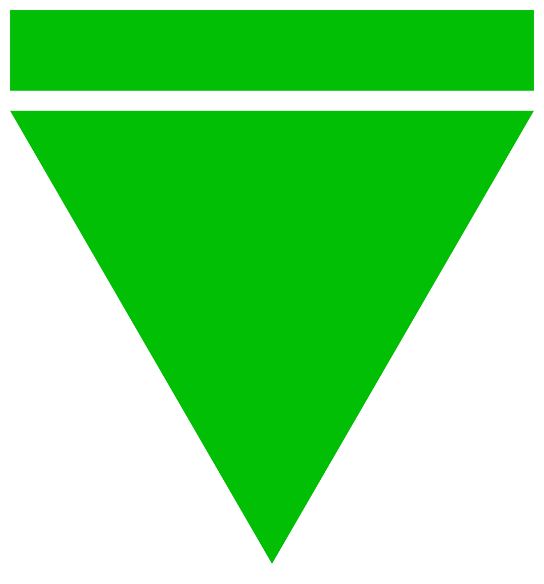
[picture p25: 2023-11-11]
Base Station/iOS Swift Code/rTalkv1/supporting/green.png

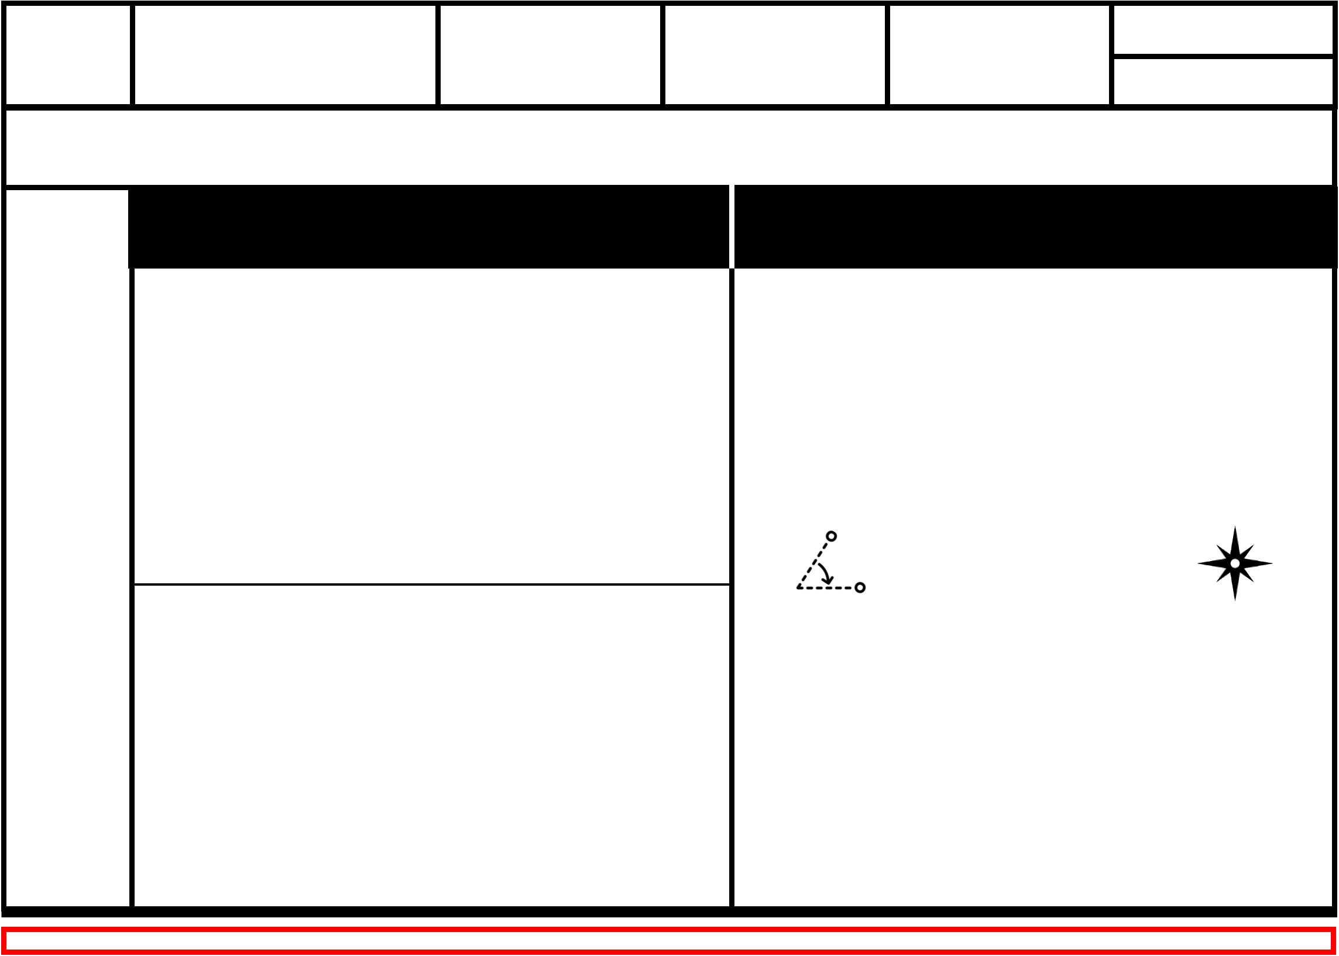
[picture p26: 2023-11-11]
Base Station/iOS Swift Code/rTalkv1/supporting/mainTemplate.png

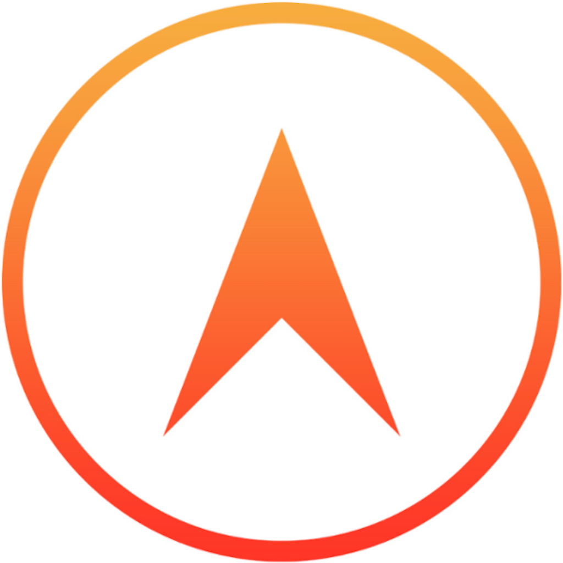
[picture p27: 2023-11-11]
Base Station/iOS Swift Code/rTalkv1/supporting/Arrow.png

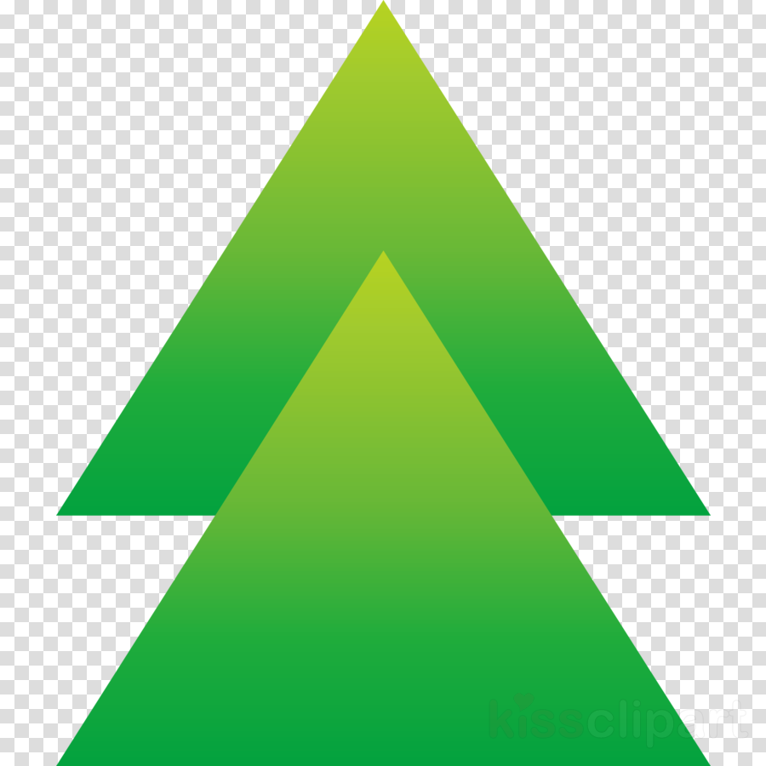
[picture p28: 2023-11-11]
Base Station/iOS Swift Code/rTalkv1/supporting/Greenlaunch.png

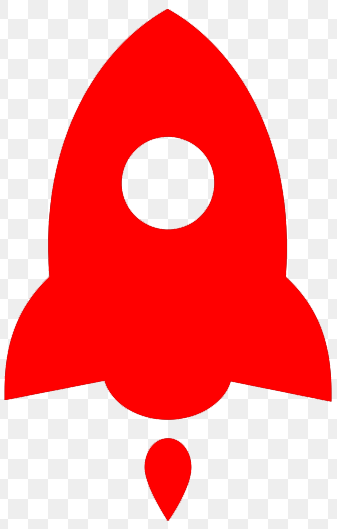
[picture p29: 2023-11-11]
Base Station/iOS Swift Code/rTalkv1/supporting/rocketpin2.png

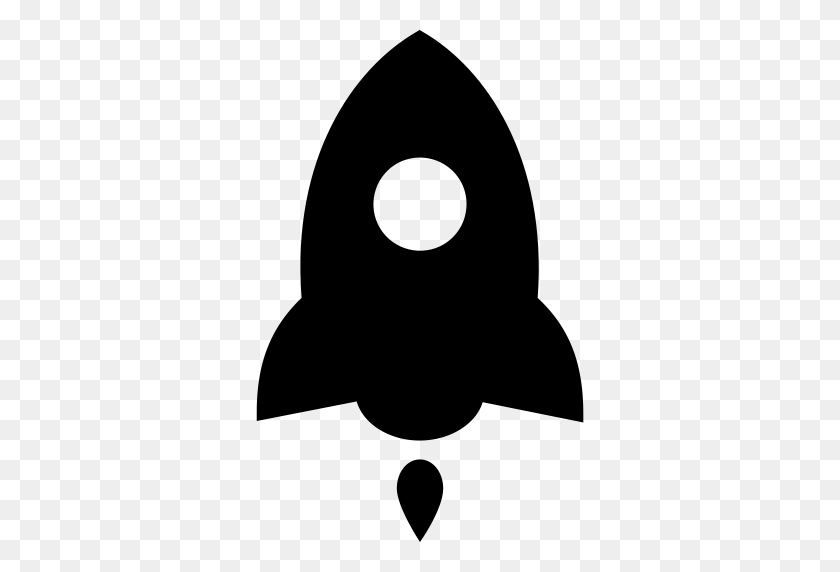
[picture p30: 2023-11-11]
Base Station/iOS Swift Code/rTalkv1/supporting/rocketpin.png

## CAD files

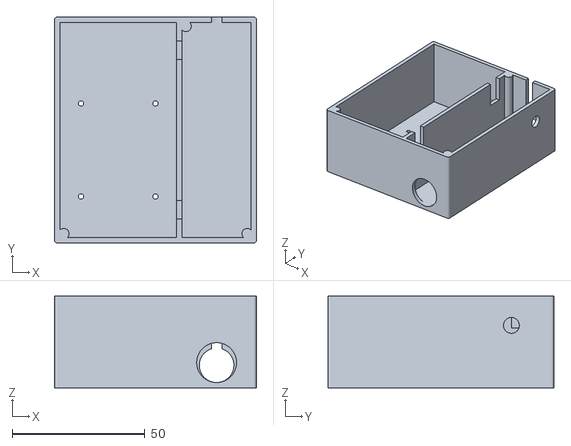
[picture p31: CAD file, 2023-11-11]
Other/3D Print Files/Base Station RadioBottom.stl
76.0 x 85.0 x 34.5

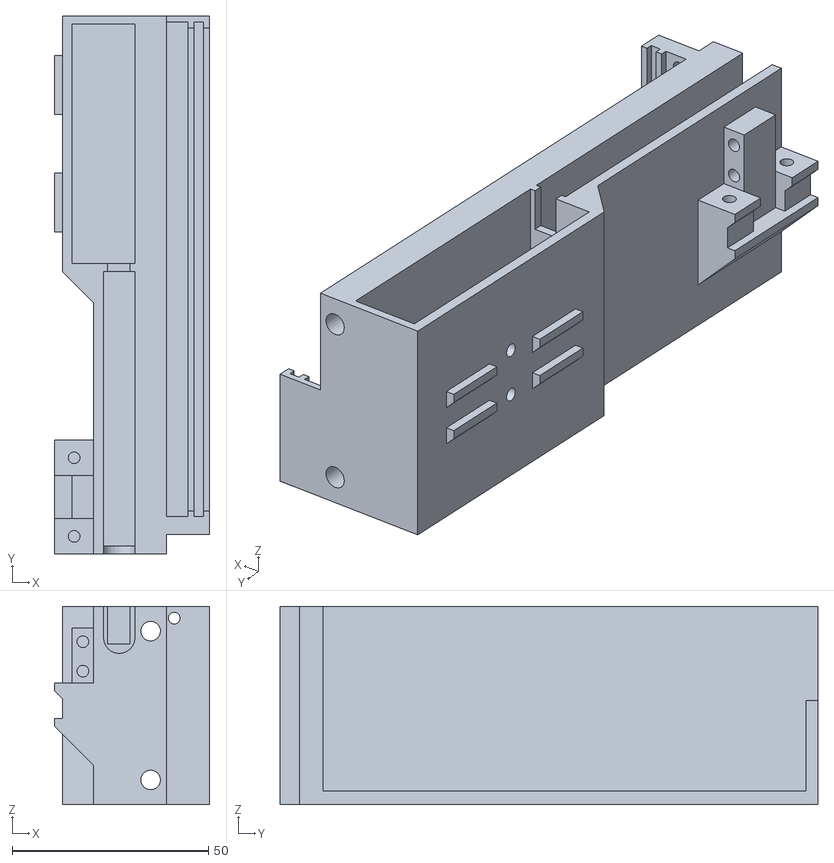
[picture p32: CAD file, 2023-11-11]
Other/3D Print Files/RocketTalk 3in Sled v5.1.stl
39.5 x 137.0 x 50.5

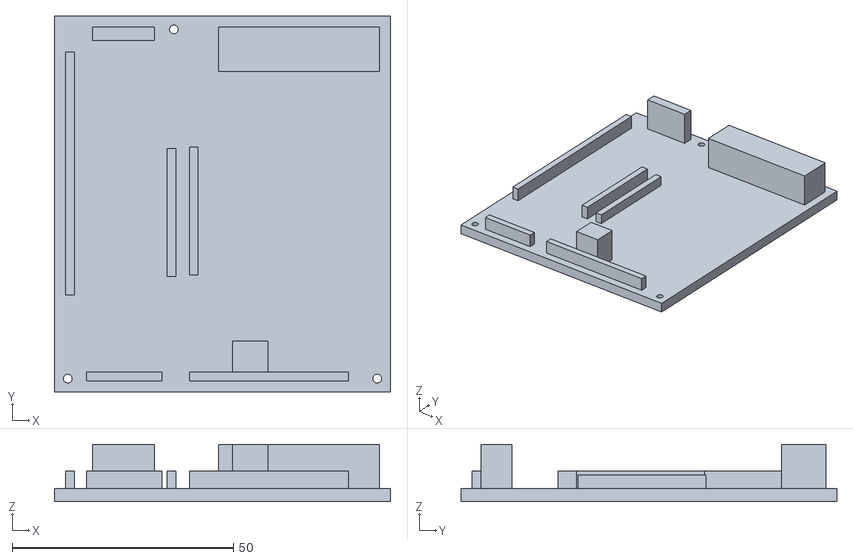
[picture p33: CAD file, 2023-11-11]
Other/3D Print Files/Base Station Radio Lid.stl
76.0 x 85.0 x 13.0

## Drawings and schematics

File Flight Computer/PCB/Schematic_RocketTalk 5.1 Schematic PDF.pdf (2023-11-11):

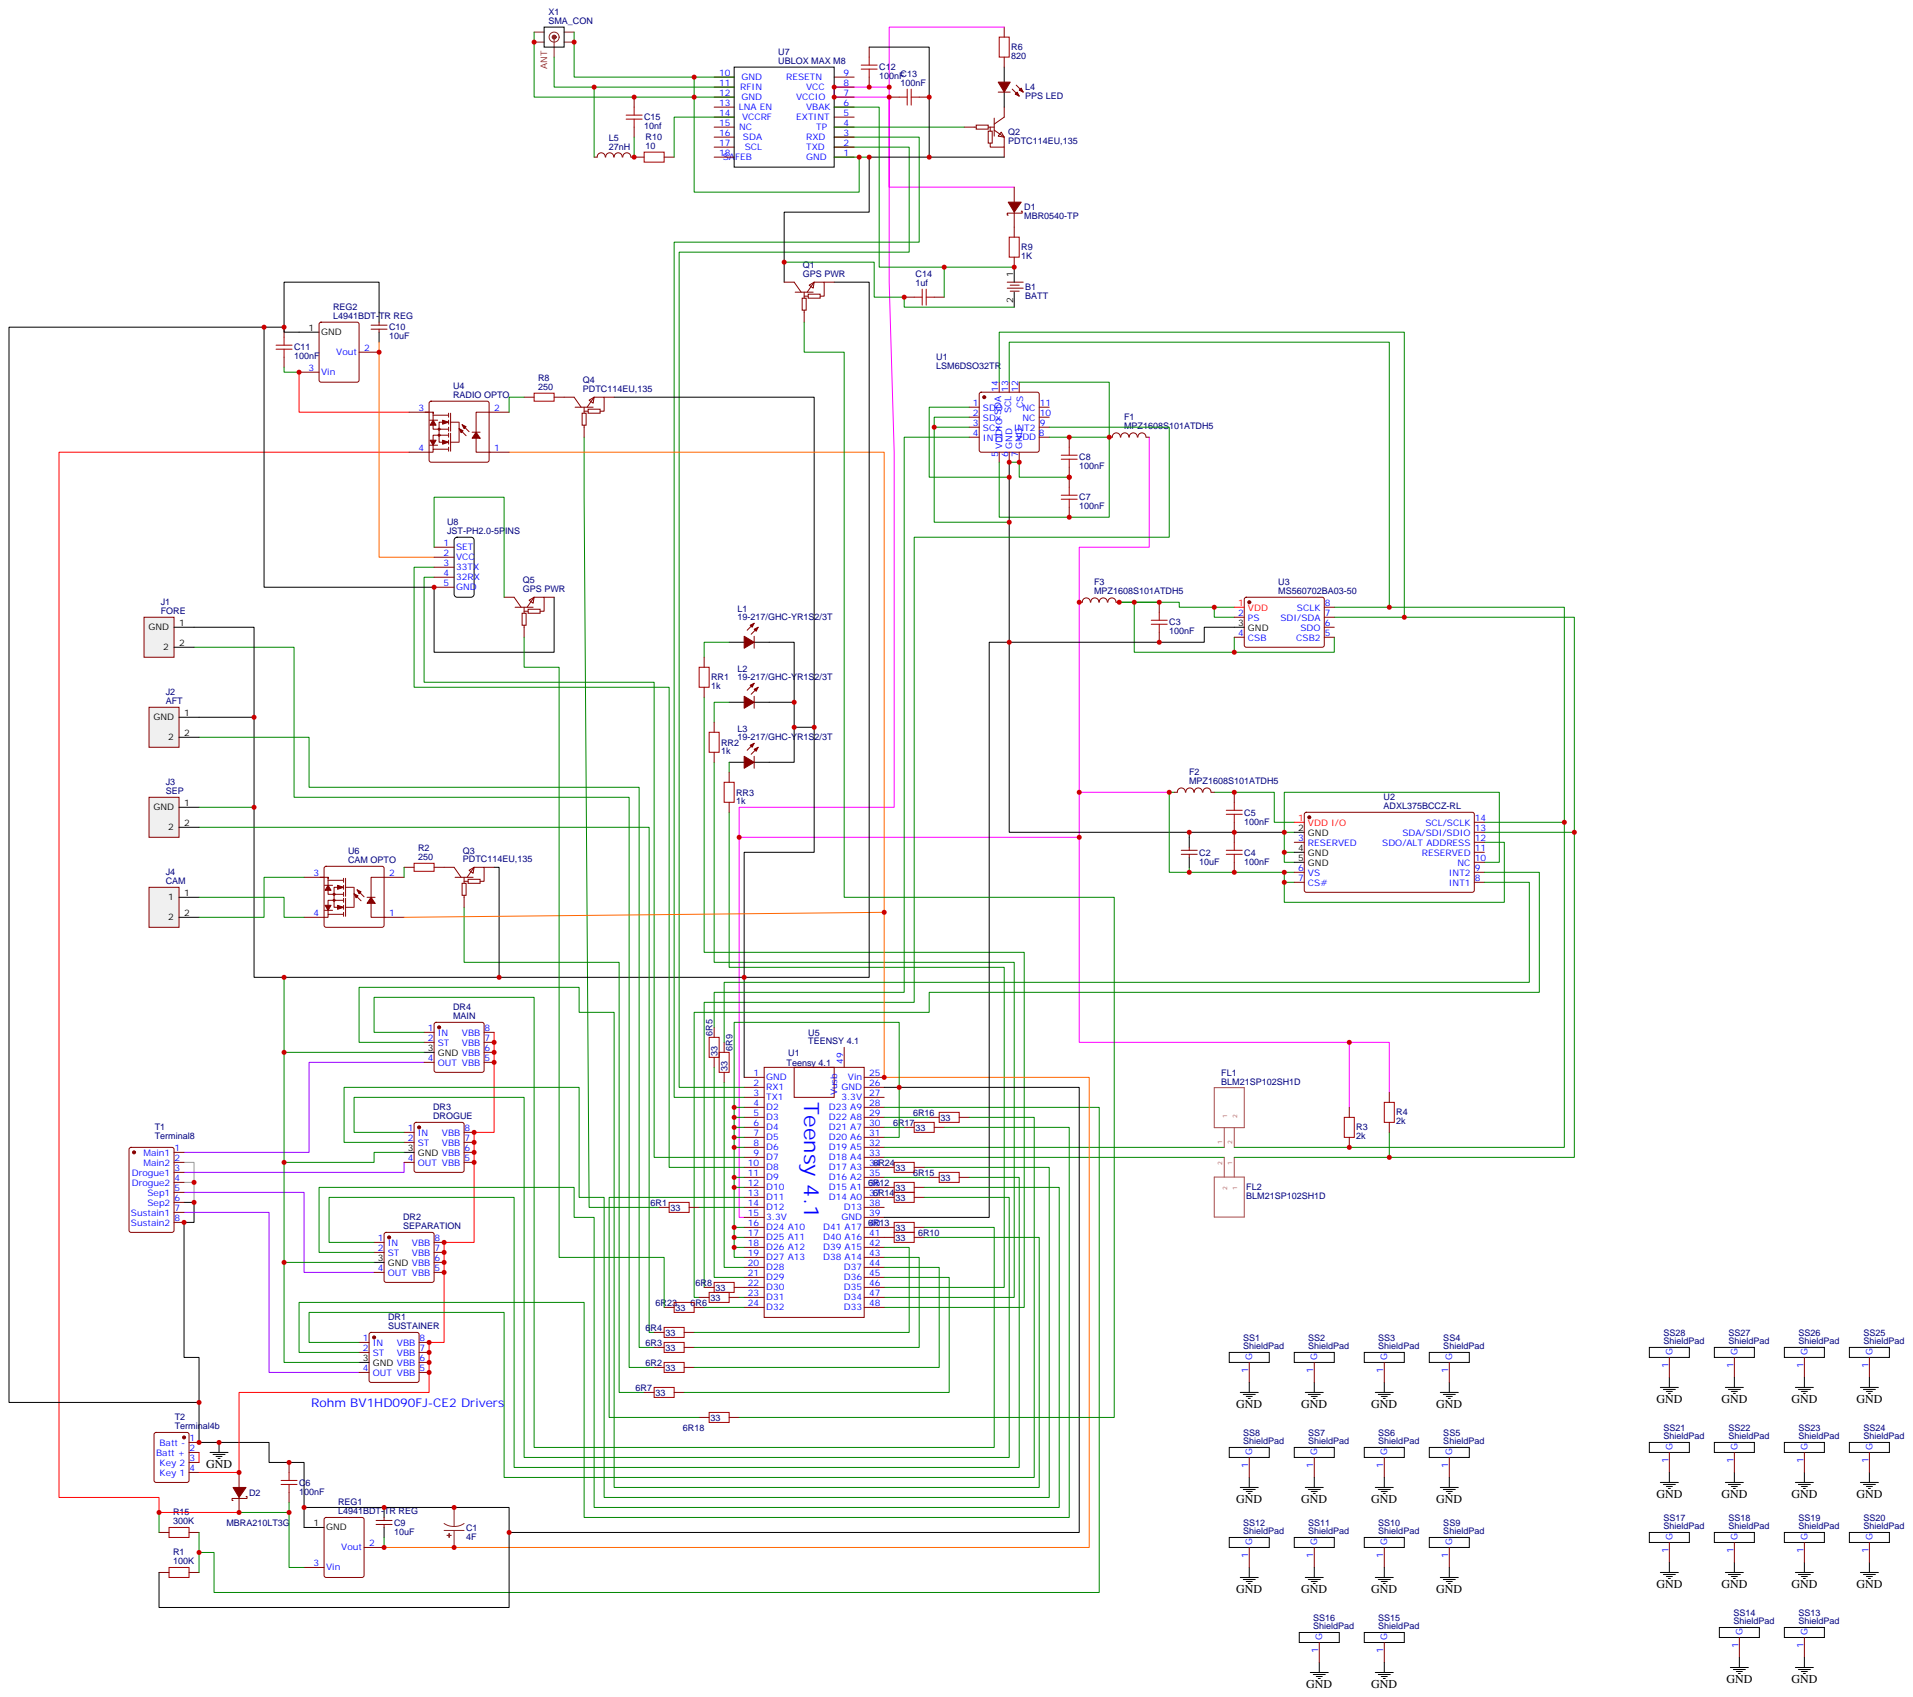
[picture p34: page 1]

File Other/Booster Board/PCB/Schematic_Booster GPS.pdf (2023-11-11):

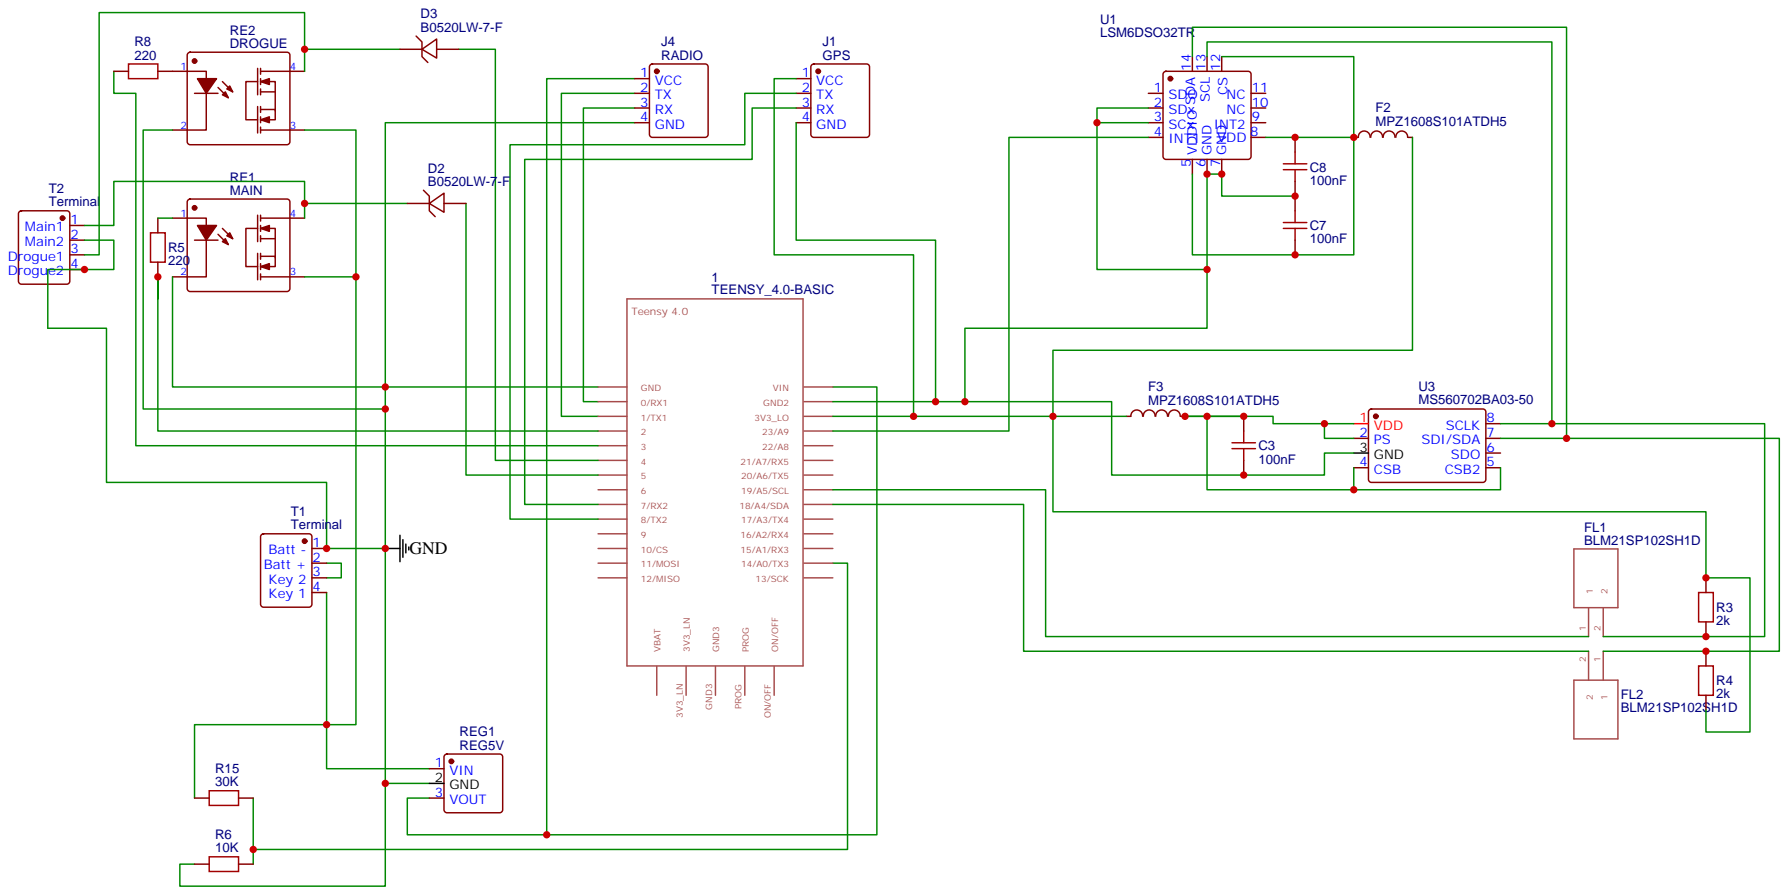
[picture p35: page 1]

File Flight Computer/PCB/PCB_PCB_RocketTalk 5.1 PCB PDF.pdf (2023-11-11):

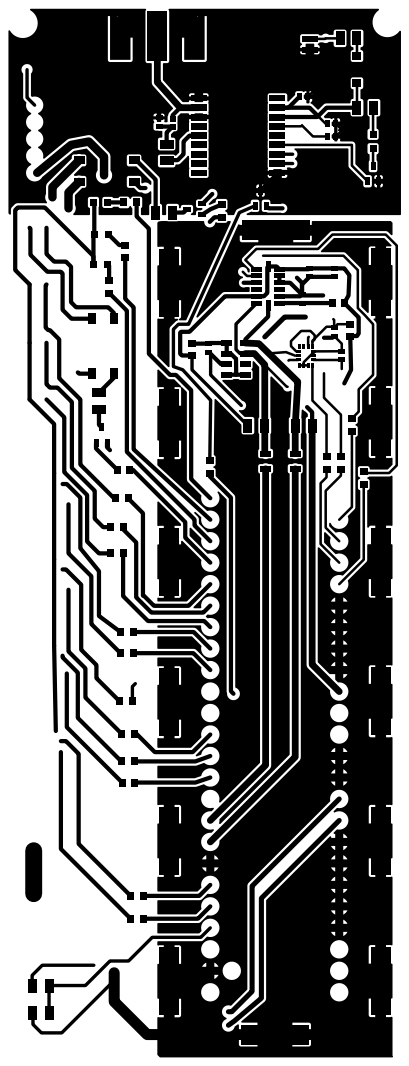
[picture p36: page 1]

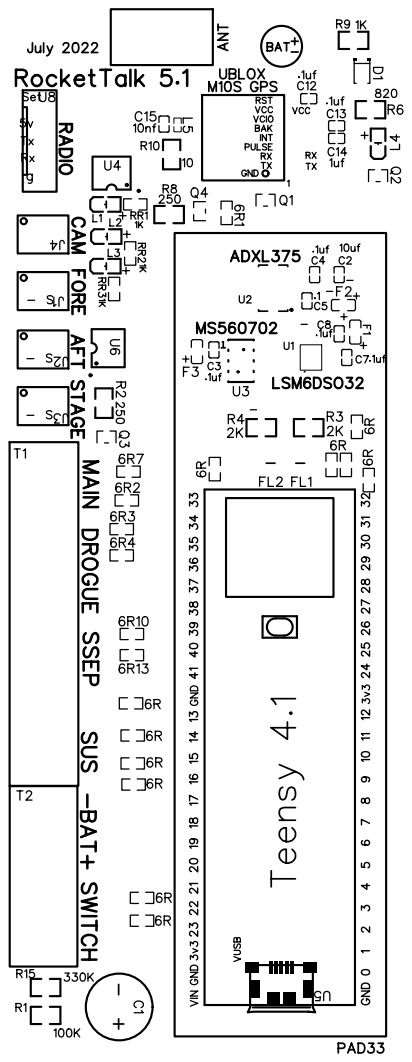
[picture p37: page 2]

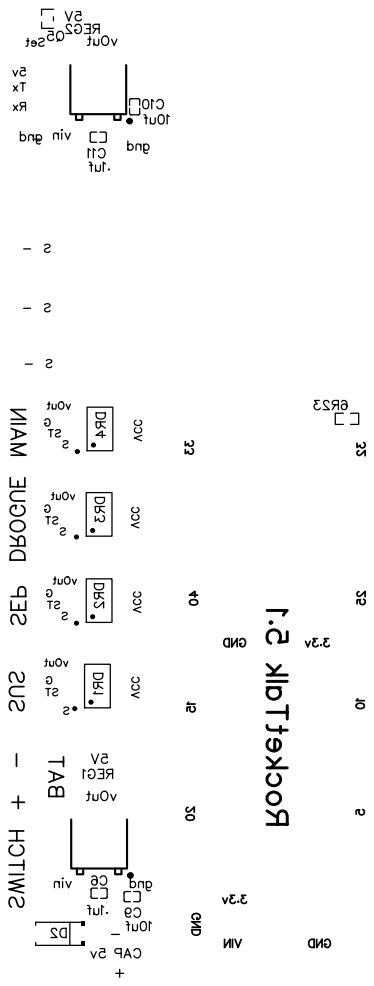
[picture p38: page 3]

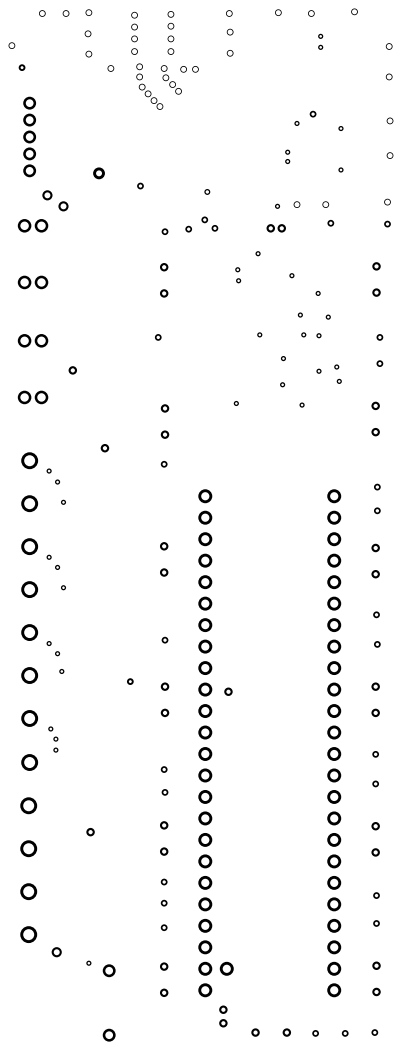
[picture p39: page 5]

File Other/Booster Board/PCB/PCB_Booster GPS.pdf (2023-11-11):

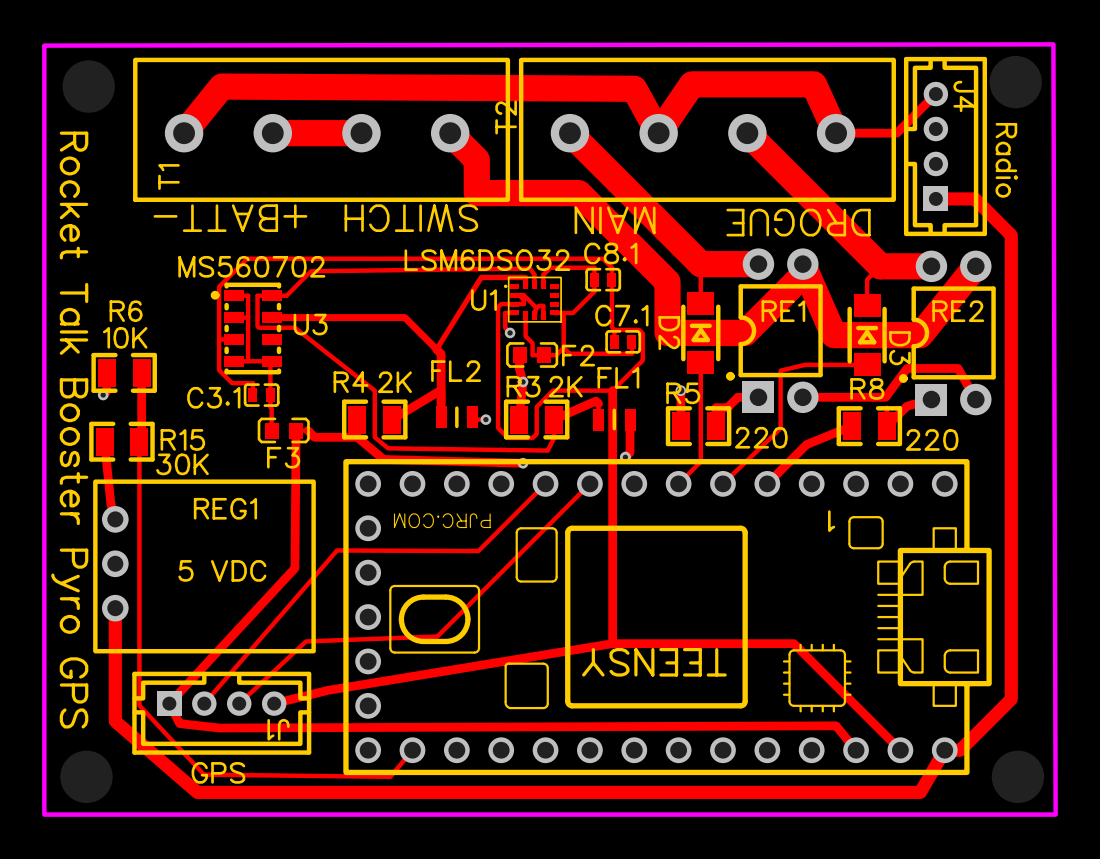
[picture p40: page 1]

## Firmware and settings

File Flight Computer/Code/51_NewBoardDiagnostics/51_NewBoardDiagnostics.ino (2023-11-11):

/* RocketTalk New Board Diagnostics 5.1
 *  
 *  Used to test all sensors, inputs and outputs on a new RT board
 *  Modified for RocketTalk Build 5.1 pins and hardware
 *  
 *  This is ALL you need for health check and calibration...
 *  
 *  
 */

  const bool sGPS = true;
  const bool sRadio = false;
  const bool sADXL = true;
  const bool sLSM = true;
  const bool sMS56 = true;
  const bool sLogging = true;


  float tempX;
  float tempY;
  float tempZ;


  #define GPSmodel 10 // (only Ublox Max-M10 logic in this code
// 5.1 pin configuration
  #define relayMain 41
  #define continuityMainPin 40
  #define relayDrogue 14
  #define continuityDroguePin 17
  #define relaySeparation 16
  #define continuitySeparationPin 15
  #define relaySustainer 22
  #define continuitySustainerPin 21
  #define fore_pin 37
  #define aft_pin 38
  #define sep_pin 39
  #define relayCamera 36
  #define led1_pin 33
  #define led2_pin 34
  #define led3_pin 35  
  #define intADXL 28
  #define int2ADXL 31
  #define radioPower_pin 12 //radio power
  #define GPSpower_pin 11 //GPS power  
  #define voltage_pinA A9 
  #define RXD1 0
  #define TXD1 1
  #define RXD2 7
  #define TXD2 8
  #define int1LSM 29
  #define int2LSM 30
  #define radioSet 32
  // also grounded pins 2,3,4,5,6,9,10,20,24,25,26,27

//Little FS flash
  #include <LittleFS.h>
  char buf[512] = "";
  char fname1[32] = "/testfile.txt";
  LittleFS_QSPIFlash myfs;
  File file, file1, file3;


//Teensy
  #include "Arduino.h"

// track the toggle logic
  bool tLED1 = false;
  bool tLED2 = false;
  bool tLED3 = false;
  bool tMain = false;
  bool tDrogue = false;
  bool tSep = false;
  bool tSus = false;
  bool tRadio = false;
  bool tGPS = false;
  bool tCam = false;



//ADXL375 Accelerometer 
  #include "ADXL375I2C.h"
  ADX375 Accel;

// For MS5607 barometer
  #include<MS5607_MB.h>
  MS5607 P_Sens;


// For LSM6DSO32 
   #include "Mike_LSM6DS.h"
   LSM6DS LSM6;  
   // QUATERNION STUFF
   #include "math.h"
   struct quaternion {
     float r;    /* real bit */
     float x, y, z;  /* imaginary bits */
    };
   quaternion masterQuaternion; 
   quaternion tempQuaternion;
   float angX, angY, angZ;

  struct configStruct {
   bool drogue = true; // fire drogue event on apogee
   bool main = true; // fire main event on descent
   float mainAltitude = 1500.0; // deploy main at 1500 feet
   bool twoStage = false; // two stage flight logic
   bool separation = false; // fire separation charge on two stage
   bool logging = true; // enable flash logging thread loop
   bool gps = false; // enable GPS checking
   bool radio = false; // enable radio checking
   bool sampling = true; //enable sampling thread loop
   bool baro = true; // enable barometer checking
   bool ADXL = true; // enable ADXL checking
   bool LSM = true; // enable LSM checking
   int machLockout = 6000;  // seconds to lock-out baro for mach
   int altitudeMin = 500;  // 500 feet minimum before pyro events
   float apogeeSpeed = 5.0; //apogee below 5fps speed
   float apogeeVelocity = 500.0; //apogee below integrated velocity of 500 on adxl
   int stagingMaxTime = 25000; // 25 seconds post launch max for staging
   float stagingSpeed = 500.0; // need to be > 500fps for staging
   int burnoutPlus = 2000; // separation two seconds after burnout
   int burnoutArm = 3000; // 3G - must hit three G before allowing burnout
   int sustainerTime = 2000; // ignite sustainer two seconds after separation
   float stagingTilt = 35.0; // 35 degree lock-out for firing sustainer
   int pyroDuration = 1000; // 1.0 second hold for pyros
   //bool invertAft = false; // used for latch switch (NO) vs normaly closed switch
   bool invertSep = false; // used for latch switch (NO) vs normaly closed switch
   
  };
  configStruct configs;



  struct workingStruct {  // working variables
    char phase[25];   // Normally should be set to STARTUP
    char callsign[10];  //Radio requires Amatuer Radio Licence
    // Testing Phase variables
    char FlightLogMaster[800];
    char RadioLogMaster[400];
    char FlightSummaryMaster[600];
    byte radioOff = 0;
    char eventString[200];
    byte logFastMode = 0; //used to keep log files open during ascent
    byte flightLogOpen = 0;
    byte gpsLogOpen = 0;
    byte radioLogOpen = 0;
    char sendFlight[150];
    char sendSummary1[250];
    char sendSummary2[250];
    char sendSummary3[250];
    char timeHeader[50];
    int summaryRepeat = 0;
    byte LaunchNumber = 0;  // used to name files on the SD card for each unique launch
    char LaunchNumberStr[16];
    unsigned long eventTimer = 0;
    byte triggerCount = 0;
    byte triggerCount2 = 0;
    byte error = 0;
    char errorMessage[100];
    byte camera = 0;
    unsigned long cameraLockout = 0;
    float voltage = 0;    
    int eLogCount = 0;
    int eLogPos = 0;
    char eventLogQ[15][200];
    int eLogLast = 0;
    int gpsLogCount = 0;
    int gpsLogPos = 0;
    char gpsLogQ[15][200];
    int gpsLogLast = 0;  
    char gpsString[200];  
    int radioLogCount = 0;
    int radioLogPos = 0;
    char radioLogQ[15][200];
    int radioLogLast = 0;  
    char radioString[200];   
    byte summaryWrite = 0;  
    int retries = 0;
    unsigned long loggingClock;
    bool loggingOK = true;
    unsigned long sampleClock;
    bool sampleOK = true;    
    float CPUtemp = 0.0;
    float CPUtempMax = 0.0;
    float accelPre = 0;
    int lockout2 = 0;
    byte eraseFlash = 0;

  };
  workingStruct working;


  struct eventStruct {  // event variables
    
    char launchTime[50];
    unsigned long launchClock;    
    bool burnout;
    float burnoutSeconds;
    unsigned long burnoutClock;
    unsigned long separationClock;
    unsigned long sustainerClock;  
    unsigned long apogeeClock;  
    unsigned long mainClock;
    unsigned long landedClock;
    unsigned long machClock;
    byte launch;
    byte apogee;
    byte landed;
    char apogeeTime[50];
    char apogeeType[5];    
    char landedTime[50];
    char launchType[5];
    char foreTime[50];
    char aftTime[50];  
    char sepTime[50]; 
    byte retries = 0;
    byte clockSet;
    int ascentSeconds;
    int descentSeconds;
    byte EventFore = 0;
    byte EventAft = 0;
    byte EventSep = 0;
    byte pyroSeparation = 0;
    byte pyroSustainer = 0;
    byte pyroMain = 0;
    byte pyroDrogue = 0;
    byte continuityMain = 0;
    byte continuityDrogue = 0;
    byte continuitySeparation = 0;
    byte continuitySustainer = 0;
    byte stagingArmed = 0;
  };
  eventStruct events;

  struct timerStruct {  // timer variables

  // logging intervals
    int eventLogInterval = 200;
    int radioLogInterval = 500;
    int gpsLogInterval = 500;

    int flightLogInterval = 1000;
  // Housekeeping
    unsigned long gpsSendTimer = 0;
    unsigned long gpsLogTimer = 0;
    unsigned long sendFlightTimer = 0;
    unsigned long voltageTimer = 0;
    unsigned long eventsTimer = 0;
    unsigned long continuityTimer = 0;
    unsigned long radioRXTimer = 0;
    unsigned long radioTXTimer = 0;
    unsigned long flightLogTimer = 0;
    unsigned long radioSendCallSignTimer = 90000;
    unsigned long pyroOffTimer = 0;
    unsigned long pyroContinuityTimer = 0;
    unsigned long loggingHealth = 0;
    unsigned long sampleHealth = 0;
    int gpsSendInterval = 5000;
    int sendFlightInterval = 4000;
    int voltageInterval = 1000; 
    int eventsInterval = 1000;
    int continuityInterval = 500;
    int radioRXInterval = 500;
    int radioTXInterval = 1200;
    int radioSendCallSignInterval = 90000;
    unsigned long PhaseTimerA;  // used for different events within each phase
    unsigned long PhaseTimerB;
    unsigned long PhaseTimerC;    
    unsigned long pyroMainTimer = 0;
    unsigned long pyroDrogueTimer = 0;
    unsigned long pyroSeparationTimer = 0;
    unsigned long pyroSustainerTimer = 0;
  };
  timerStruct timers;
  
  
  struct LSMStruct {  //LSM6DSO32 variables
    int count;
    float x, y, z;   
    float linZ;
    float avgZ;
    float tempAvgZ;
    float maxZ;
    float minZ;
    float velocity;
    float velocityLast; 
    byte apogee;    
    unsigned long last;   
    float launchMaxZ;  
    int bias;
    int tempbias;
    int biasCount;     
    byte burnout = 0;    
    byte burnoutArm = 0;   
    
    float gX, gY, gZ;  // raw avg
    float tilt = 0.0;
    float tiltMax = 0.0;
    float tiltMaxLaunch = 0.0;
    float yaw;
    float pitch;
    float roll;
  };
  LSMStruct LSM6D;

// global for the barometer tracking 
  struct baroStruct {
    float Altitude = 0.0;
    float AltitudeMax = 0.0;
    float tempAltitude = 0.0;
    float lastAltitude;
    float Baseline = 0.0;
    float TempF;    
    float TempMax;    
    float Speed = 0.0;  // speed in FPS
    float LandedSpeed = 0.0;
    float SpeedMax = 0.0; 
    float Pressure = 0.0;
    float Tempraw = 0.0;
    float Altraw = 0.0;
    unsigned long launchDetectDelay;
    byte apogee;  
    int count;  
    byte launch;
  };
  baroStruct baro;

  //ADXL375 Accelerometer 
  #include "ADXL375I2C.h"
  struct adxlStruct {  // ADXL Accelerometer Variables
    int count;
    float x, y, z;   
    float linZ;
    float avgZ;
    float tempAvgZ;
    float maxZ;
    float minZ;
    float velocity;
    float velocityLast;    
    int bias;
    int tempbias;
    int biasCount;    
    byte apogee;    
    unsigned long last;   
    float launchMaxZ;  
    byte burnout = 0;
    byte burnoutArm = 0; 
    byte launch = 0;
  };
  adxlStruct adxl;

  // GPS
  struct gpsDataStruct {  // GPS variables
    char vGNRMC[200]; 
    char vGNGGA[200]; 
    char vGNGNS[200]; 
    char gpsDate[15];
    char gpsTime[15];
    char fix[15];
    char quality[15];
    char latRaw[15];
    float latDec;
    float longDec;
    char longRaw[15];
    char longFriendly[15];
    char latFriendly[15];
    char gpsAltitudeMeters[15];
    char gpsAltitudeFeet[15];
    char altitudeAGL[15];
    char gpsSpeed[15];
    char angle[15];
    char sat[15];
    char posMode[15];    
    float baseline;
    float maxAGLfeet;
    char gpsLogLine[300];
    char gpsSendLine[150];
    int gpsStatus;
  };
  gpsDataStruct gpsData;
  bool GPSgood = false;
  
  char aGNRMC[20][20]={0x0}; //for parsing
  char aGNGGA[20][20]={0x0};
  char aGNGNS[20][20]={0x0};
  int fldcnt=0; //for parsing

// *** Radio Setup
  char radioHeader[5];
  char radioMessage[150];
  char radioMessageS[200];
  int newWord = 0;
  char theWord[100];

//added for send queue
  char rSend[15][300];
  byte rSendCount = 0;
  byte rSendLast = 0;
  byte rSendPos = 0;
  char vFullMessageR[300];

  struct debugStruct {
    int adxlCount;
    int baroCount;
    int LSM6DCount;
    int logCount;
    int count1;
    int count2;
    unsigned long debugTimer;
    unsigned long adxlStart;
    unsigned long baroStart;
    unsigned long LSMstart;
    int adxlTime;
    int baroTime;
    int LSMtime;
    int GPScount;
    int GPSquality; //99 timeout, 0 none, # sats
    int gpsTime;
  };
  debugStruct debugVars;

// For threading
  int id_logging, id_sampling;

// For the flash memory
//  #include <LittleFS_NAND.h>
  #include <LittleFS.h>
  #include <stdarg.h>
  uint64_t fTot, totSize1;
  
  #include <TimeLib.h>  // for logging time


// Temperature from CPU
  extern float tempmonGetTemp(void);  

// just for SD
  #include "SD.h"
  #include <SPI.h> 
  File tempFile;

//************************************************************************************************************************************************************  SETUP
//************************************************************************************************************************************************************  SETUP
void setup() {

// Pin setup
  pinMode(radioPower_pin, OUTPUT);  digitalWrite(radioPower_pin, LOW);
  pinMode(radioSet, OUTPUT);  digitalWrite(radioSet, LOW);
  pinMode(GPSpower_pin, OUTPUT);  digitalWrite(GPSpower_pin, LOW);
  pinMode(relayMain, OUTPUT);  digitalWrite(relayMain, LOW);
  pinMode(relayDrogue, OUTPUT);  digitalWrite(relayDrogue, LOW);
  pinMode(relaySustainer, OUTPUT);  digitalWrite(relaySustainer, LOW);
  pinMode(relaySeparation, OUTPUT);  digitalWrite(relaySeparation, LOW);
  pinMode(relayCamera, OUTPUT);  digitalWrite(relayCamera, LOW);
  pinMode(led1_pin, OUTPUT);  digitalWrite(led1_pin, LOW);
  pinMode(led2_pin, OUTPUT);  digitalWrite(led2_pin, LOW);
  pinMode(led3_pin, OUTPUT);  digitalWrite(led3_pin, LOW);
  pinMode(fore_pin, INPUT_PULLUP);
  pinMode(aft_pin, INPUT_PULLUP);
  pinMode(sep_pin, INPUT_PULLUP);
  pinMode(intADXL, INPUT);
  pinMode(int2ADXL, INPUT);  
  pinMode(int1LSM, INPUT  ); //only set to input - now using int2
  pinMode(int2LSM, INPUT_PULLUP);
  pinMode(voltage_pinA, INPUT);
  pinMode(continuityMainPin, INPUT_PULLUP);   
  pinMode(continuityDroguePin, INPUT_PULLUP);   
  pinMode(continuitySustainerPin, INPUT_PULLUP);   
  pinMode(continuitySeparationPin, INPUT_PULLUP);   
  // Grounded pins for RFI:  2,3,4,5,6,9,10,17,20,24,25,26,27,32
  pinMode(2,INPUT);pinMode(3,INPUT);pinMode(4,INPUT);pinMode(5,INPUT);pinMode(6,INPUT);
  pinMode(9,INPUT);pinMode(10,INPUT);pinMode(20,INPUT);pinMode(24,INPUT);
  pinMode(25,INPUT);pinMode(26,INPUT);pinMode(27,INPUT);
  pinMode(13,OUTPUT); digitalWrite(13, LOW);//internal LED

  
  delay(4000);
  Serial.begin(115200);
  delay(100);
  Serial.println("RocketTalk New Board Diagnostics and Health Check v5.1 hardware");
  Serial.println(" ");Serial.println(" ");



  // Initialize GPS Serial
  if(sGPS) {
      Serial1.begin(9600);
  }

  printCommands();

}

//************************************************************************************************************************************************************  MAIN LOOP
//************************************************************************************************************************************************************  MAIN LOOP

void loop() {

  char chIn = 255;
  if ( Serial.available() ) {
    do {
      if ( chIn != '1' && chIn != '2' && chIn != '3' && chIn != '4' && chIn != '5' && chIn != '6' && chIn != '7' && chIn != '8' && chIn != '9' && chIn != 'a' && chIn != 'b' && chIn != 'c' && chIn != 'd' && chIn != 'e' && chIn != 'f' && chIn != 'g' && chIn != 'h' && chIn != 'i' && chIn != 'j' && chIn != 'k' && chIn != 'l' && chIn != 'm' && chIn != 'n' && chIn != 'o' && chIn != 'p' && chIn != 'q' && chIn != 'r' && chIn != 's' )
        chIn = Serial.read();
      else
        Serial.read();
    }
    while ( Serial.available() );
  }



  
  if ( chIn == '1' ) {
     checkSensors();
     printCommands();
  }
  if ( chIn == '2' ) {
     I2Cscan();
     printCommands();
  }
  if ( chIn == '3' ) {
     GPStest();
     printCommands();
  }
  if ( chIn == '4' ) {
     flashLogging();
     printCommands();
  }
  if ( chIn == '5' ) {
     checkVoltage();
     printCommands();
  }
  if ( chIn == '6' ) {
     checkContinuity();
     printCommands();
  }
  if ( chIn == '7' ) {
     checkEvents();
     printCommands();
  }
  if ( chIn == '8' ) {
     checkTemp();
     printCommands();
  }
  if ( chIn == '9' ) {
     radioTest();
     printCommands();
  }


  
  if ( chIn == 'a' ) {
     toggleA();
     printCommands();
  }

  if ( chIn == 'b' ) {
     toggleB();
     printCommands();
  }
  if ( chIn == 'c' ) {
     toggleC();
     printCommands();
  }
  if ( chIn == 'd' ) {
     toggleD();
     printCommands();
  }
  if ( chIn == 'e' ) {
     toggleE();
     printCommands();
  }
  if ( chIn == 'f' ) {
     toggleF();
     printCommands();
  }
  if ( chIn == 'g' ) {
     toggleG();
     printCommands();
  }
  if ( chIn == 'h' ) {
     toggleH();
     printCommands();
  }
  if ( chIn == 'i' ) {
     toggleI();
     printCommands();
  }
  if ( chIn == 'j' ) {
     toggleJ();
     printCommands();
  }
  if ( chIn == 'k' ) {
     calibrateADXL();
     printCommands();
  }
  if ( chIn == 'l' ) {
     calibrateLSMa();
     printCommands();
  }
  if ( chIn == 'm' ) {
     calibrateLSMg();
     printCommands();
  }
  if ( chIn == 'n' ) {
     calibrateBaro();
     printCommands();
  }
  if ( chIn == 'o' ) {
     quaternionDrift();
     printCommands();
  }

  if ( chIn == 'p' ) {
     formatFlash();
     printCommands();
  }
  if ( chIn == 'q' ) {
     eraseFlash();
     printCommands();
  }

  
  if ( chIn == 'r' ) {
     printFlashDirectory();
     printCommands();
  }
  if ( chIn == 's' ) {
     copy2SD();
     printCommands();
  }


  
}


void printCommands() {
  Serial.println("  ");
  Serial.println("----------------------------------------------------------------------------------------------------------------------------");
  Serial.println("COMMANDS:");
  Serial.println("   1-Check Sensors,  2-I2C Scan, 3-Check GPS, 4-Check flash logging, 5-voltage, 6-Continuity, 7-Event pins, 8-Temp, 9-Radio Test ");
  Serial.println("   TOGGLE:  a-LED1, b=LED2, c=LED3, d=pyro MAIN, e=pyro DROGUE, f=pyro SEP, g=pyro SUS, h=Radio Power, i=GPS power, j=Camera");
  Serial.println("   CALIBRATE:  k-ADXL, l-LSM-Accel, m-LSM-Gyro  n-Baro  o-quant drift");  
  Serial.println("   FLASH:  p-Low Format, q-Quick Erase, r-Directory, s-copy to SD");  
  Serial.println("----------------------------------------------------------------------------------------------------------------------------");  
  Serial.println("  ");
}

void I2Cscan() {

 byte error, address;
  int nDevices;
  Serial.println("Scanning I2C Bus...");
  Wire.begin();
  delay(1000);
  
  nDevices = 0;
  for(address = 1; address < 127; address++ )
  {
    // The i2c_scanner uses the return value of
    // the Write.endTransmisstion to see if
    // a device did acknowledge to the address.
    Wire.beginTransmission(address);
    error = Wire.endTransmission();
 
    if (error == 0)
    {
      Serial.print("I2C device found at address 0x");
      if (address<16)
        Serial.print("0");
      Serial.println(address,HEX);
 
      nDevices++;
    }
    else if (error==4)
    {
      Serial.print("Unknown error at address 0x");
      if (address<16)
        Serial.print("0");
      Serial.println(address,HEX);
    }    
  }
  if (nDevices == 0)
    Serial.println("No I2C devices found\n");
  else
    Serial.println("done\n");
  Wire.end(); 

  
}
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
